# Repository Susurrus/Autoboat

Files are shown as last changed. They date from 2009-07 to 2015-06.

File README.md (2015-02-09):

Autoboat
========

This repository contains code used for running the Autoboat, a 20' robotic surface vessel currently in development at the University of Santa Cruz under the directive of Professor Gabriel Elkaim. This respository is therefore likely to be of little interest to outsiders, though much of the support code is fairly modular. Groundstation software for this vessel is provided via the QGroundControl project and is not contained within this repository.

File layout
-----------
 * CAD - Contains CAD designs of both mechanical and electrical systems. The mechanical systems have been modeled in SolidWorks 2010 while the electrical schematics have been generated using Eagle 6.
 * Code - This contains the software used for controlling the boat. Primarily Simulink and C control its operation and MATLAB and Python scripts assist in data parsing and analysis
 * Documentation - Various documents regarding this project are stored in this directory.

Main project
------------

The main project code is housed within /Code/Primary_node/primary_node.mdl and /Code/basic\_model/Boat\_sim.mdl, both Simulink 2011b models.

Boat_sim.mdl provides a simulator for testing my vehicle/environmental model and the vehicle controllers. It can run solely on a computer or via a UDP port provide the vehicle/environmental simulation to an external controller for use in Hardware-in-the-Loop (HIL) testing. Relies on the MicroSimulink library (<https://github.com/Susurrus/MicroSimulink-Library>).

primary_node.mdl contains all of the controller logic for the primary controller. It is organized as hardware dependent code that wraps the main controller block that is shared with Boat_sim.mdl (via the make.m script). This is designed to run aboard a CANode with the dsPIC33FJ256GP710A onboard along with a custom shield for providing connections to peripherals. It depends on both the MicroSimulink library (<https://github.com/Susurrus/MicroSimulink-Library>), Lubin's PIC blockset (<http://www.kerhuel.eu/wiki/Simulink_-_Embedded_Target_for_PIC>), and the ECAN blockset (<https://github.com/Susurrus/ECAN_dspic>). All of these dependencies must be correctly installed and on the path along with Microchip's xc16 compiler for this project to compile to an executable.

The toolboxes required by the various models are the Aerospace Blockset, MATLAB, MATLAB coder, Simulink, and Simulink Coder.

Code generation of the MATLAB projects requires a supported compiler [www.mathworks.com/support/compilers/R2011b] crosoft's Visual Studio 2010 is also required in order to compile the project or the Windows SDK 7.1 or newer. Both are available for free online.

In addition to these Simulink libraries, the MAVLink C library for the SeaSlug must be installed. Download it from <https://github.com/mavlink/mavlink> into the same directory that this repository is contained in so that it looks like:
/MicroSimulink-Library
/ECAN_dspic
/Autoboat
/mavlink

You'll need Python 2.6+ to run the MAVLink generator from within the mavlink directory:

```$ python mavgen.py --lang=C --wire-protocol=1.0 -o include ../Autoboat/Code/Libs/MAVLink/seaslug.xml```

This will put the MAVLink code for the SeaSlug dialect into ```/mavlink/include``` where it can be referenced by primary_node.mdl.

The current version of MAVLink will not compile with the xc16 compiler unless the ```stdint.h``` header file within the xc16 includes directory is duplicated as an ```inttypes.h``` file.
 
Further documentation
---------------------

A wiki has been hosted to provide details on this project at <http://byron.soe.ucsc.edu/autoboat/wg2/>.

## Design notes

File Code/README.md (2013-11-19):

1. Introduction
===============

This folder contains various projects containing code pertaining to the SeaSlug.

2. Requirements
===============
Software:
 * MATLAB/Simulink
     * Instrument control toolkit/blockset
     * Aerospace toolkit/blockset
     * Embedded coder, MATLAB coder, Simulink coder
     * [uSimLib](https://github.com/Susurrus/MicroSimulink-Library) and in the path
     * [Lubin Kerhuel's Simulink blockset](http://www.kerhuel.eu/wiki/Simulink_-_Embedded_Target_for_PIC) and in the path
     * Added to the path: `/Code/Libs/MATLAB`, `/Code/primary_node`, `/Code/basic_model`, `/Code/Scripts/MATLAB`
 * Microchip's MPLAB X (newest)
 * Microchip's XC16 (newest)

Hardware
 * CANode (contact asl.soe.ucsc.edu) with dsPIC33EP256MC502

3. Projects
===========

basic_model
-----------
Implements several simulator models along with Plant.mdl, the plant used for simulating the boat. Utilizes a crude inverse-bicycle model. To run these `/Code/primary_node/` must be on the MATLAB path. The `/Code/basic_model` folder must also be on the path for opening these models when the current working directory is not this folder.

HIL_node
--------
Provides a CAN interface with the basic_model simulator via a serial connection (that needs a serial-to-UDP bridge). Emulates many of the other nodes in order to fool the primary_node into normal operations. Written in all C.

Imu_node
--------
Provides a CAN interface to the Tokimec VSAS-2GM IMU+GPS interfacing over RS232. Broadcasts all incoming IMU data via CAN using the same data packets the VSAS-2GM would normally use over CAN. Utilizes Lubin's blockset for generating C code from Simulink.

Libs
----
Contains all shared code used by this project sorted by language. Also contains input files for some libraries, like MAVLink.
 
Paper_sim
---------
A simulation model built off of P�rez and Blanke 2002. Relies on many coefficients that need to be found experimentally, so it's not very accurate right now. Hopefully this will be the approach taken for the final boat model.

Power_node
----------
This runs on a CAN node and translates the sensor values for the current/voltage sensor on the main power rail into CAN messages. These are then processed by the primary controller node. Written entirely in C.

Primary_node
------------
This node implements the same controller as the basic_model simulator. It has an onboard interface to an analog power sensor, but otherwise all vessel communications are done over CAN. Its groundstation output is via the UART connector on the CANode.

Compiling this code involves generating the code for controller.mdl using Simulink (requires github.com/Susurrus/MicroSimulink-Library). Then all necessary C code is compiled using MPLAB X.

Additional requirements for compiling this node:
 * The XC16's `stdint.h` file should be duplicated as the `inttypes.h` file in order for MAVLink to compile.
 * It requires a SeaSlug-compiled MAVLink library, generated by the mavgen.py tool from github.com/mavlink/mavlink using the .xml file in `/Code/Libs/MAVLink`.
 * A heap size of 1024 bytes should be specified when the project is compiled in MPLAB X.

RC_node
-------
Provides a CAN interface for an RC receiver using a CANode. It also has a custom shield providing a plug-in interface for Spektrum's AR6100e receiver. Relies on Lubin's blockset for code generation.

Rudder_node
----------------
Integrates with the rudder (a stepper motor driver board, potentiometer position sensor, and port/starbord limit switches) and provides a CAN interface to it. Handles calibration as well. This has the same compilation requirements as the RC node.

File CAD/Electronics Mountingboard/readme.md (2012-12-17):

# Electronics Mounting Board

This directory contains Solidworks 2012 CAD files for a mounting board for the various onboard electronics onboard the boat. It fits inside a Wiegmann BN4161406SS electronics box. This includes a large capacitor, 3 CAN nodes providing various functions, and an ACS300 brushless DC motor driver board. Some screw terminal blocks also have mounting holes (they're all from Blue Sea Systems).

It was designed to be cut out of a non-conductive 1/4" material. The Corel Draw DXF file is included for use with a laser cutter.

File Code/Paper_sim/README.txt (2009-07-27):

This is a boat model based on the following paper:

Pérez and Blanke. Mathematical Ship Modeling for Control Applications.  (2002) pp. 1-22

This model uses constants defined in boat_constants.m as the coefficients for the boat dynamics. Most of the 
constants are currently made up or loosely approximated (eg. the intertias are based on a cuboid roughly the 
volume of the boat).

Currently the model tops out at 1.93m/s when at maximum throttle. This model is stable.

There are many properties of the boat that need to be experimentally determined to improve this model and are 
listed under the experimental constants in boat_consants.m.

The model Currently only implements a couple of forces/moments:

Drag (Using wg1 sim model)
Thrust (Using wg1 sim model)
Rudder moment (using wg1 sim model)

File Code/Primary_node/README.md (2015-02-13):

## Compilation

Compilation is done in two stages: first by MATLAB/Simulink and finally by MPLAB X. The first stage involves code generation (see the project README for software requirements). The second stage with MPLAB X involves compiling the resultant MPLAB X project and manually setting the Memory Model to 'large'.

This project requires both the '/Code/Libs/MATLAB' folder and the MicroSimulink-Library project be added to MATLAB's path to compile.

### MPLAB X Project Settings
 1. Add the following directories to the include search path: 
   * `/Code/Libs/C`
   * `/Code/Libs/MAVLink/seaslug`
   * `/Code/primary_node`
   * `/Code/primary_node/controller_ert_rtw`
 2. Specify the large code & large data model
 3. Add "MAVLINK_ALIGNED_FIELDS=0" as a C macro
 4. Add MAVLINK_SEPARATE_HELPERS as a C macro
 4. Add all *.c under `controller_ert_rtw' to the project.
 5. Add all *.c files in `/Code/primary_node`.
 6. Add missing files as reported by the compiler in `/Code/Libs/C`
 7. OPTIONAL: Add traps.c if weird resets occur to see which error is triggering
 
Note, when regenerating MAVLink, there may arise a conflict between the mavlink_helpers.c file we provide and the function prototypes provided in protocol.h. The mavlink_helpers.c file will need to be adjusted by just copying over the functiond definitions from mavlink_helpers.h.

### dsPIC33E versus dsPIC33F

Switching between these processors requires the following changes:
 1. Choose the proper DEES_*.s file based on the processor type selected.

## Functionality

### MAVLink corruption compensation
The UART1 transmission is connected to UART2 reception at the pin-level on the PIC. A separate MAVLink decoding process is run on this and the processor logs when its output stream has become corrupted, resets the UART1 transmission hardware and outputs a STATUSTEXT MAVLink message with the time this occurred.

Additionally, while the data stream is corrupted, pin RB0 is set high, so a low value indicates a valid MAVLink stream.

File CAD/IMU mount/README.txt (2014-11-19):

This is a mounting plate for the Tokimec VSAS-2GM IMU onto the wooden IMU shelf in the forward compartment of the SeaSlug. 5/8" #8 wood screws fit in the outer-most screw holes securing the plate to the boat. M6 Allen-head bolts screw up into a locknut above the Tokimec.

This can be trivially lasercut out of acrylic. The #8 screws will need to be recessed and same with the boltheads for the Tokimec.

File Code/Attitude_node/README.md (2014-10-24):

Add all files in this directory along with:
  /Code/Libs/C/{CanMessages.c, CircularBuffer.c, Ecan1.c, MessageScheduler.c, Node.c, Timer2.c, Stack.s, Traps.c, Uart1.c}
  /Code/Libs/MPU60xx/*.c

You need to make sure `git submodule init` and `git submodule update` were run and that `/Code/Libs/MPU60xx` exists with code inside.

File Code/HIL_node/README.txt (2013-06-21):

This code implements a CAN to UDP bridge for use in HIL simulation. It runs atop  a CAN node with a ENC28J60 Ethernet shield. It emulates all CAN-based sensors and sits between the primary controller for the SeaSlug and its Simulink simulation.

This code builds on the TCP/IP stack provided by Microchip and available directly from them. While none of their library code has been modified for this project, it has been included here to simplify things.

# Usage
This code should be compiled for the CAN node and programmed onboard. That node should have an ethernet shield and be connected to a laptop (it has a DHCP server so IP address assignment is automatic) as well as to the primary controller node via CAN.

# Compilation

Compilation is done completely via Microchip's MPLAB X IDE and the XC16 compiler.

Required include directories:
 ./TCPIP
 .
 ../Libs/C 

Required source files:
 ./*.c
 ./TCPIP/TCPIP Stack/*.c
 ../Libs/C/[Acs300,CanMessages,CircularBuffer,Ecan1,MessageScheduler,Nmea2000,Nmea2000Encode,Node,Rudder,Timer2,Timer3,Timer4].c

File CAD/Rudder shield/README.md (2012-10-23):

This board is designed for V2.x of the CAN node that exists in the ASL repository. I provides connections for integrating an analog potentiometer (with a 21Hz lowpass filter on it) and two open-drain limit switches. Additionally it has a connection for a stepper motor driver board.

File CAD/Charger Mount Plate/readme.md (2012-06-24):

# Charger Mounting Plate

This directory contains the Solidworks 2008 CAD designs for a electronics mounting board for use in the bow of the Autoboat. A Corel Draw file is included for the mounting board itself for use with a laser cutter.

This board is designed to be laser cut out of 1/4" material, preferably something that doesn't respond to moisture like acrylic (not MDF). It's used for mounting both a Wiegmann BN4161406SS electronics box as well as the Dual Pro Professional Series Quad Pro battery charger. It is designed to be mounted in the boat with the charger mounted on the left side. 

This board should then be attached to two 2x4s that run along the entire width with the 4" against the MDF. For each of the mounting holes in the MDF, 3/4" holes should be drilled through the 2x4s to allow for a socket wrench.

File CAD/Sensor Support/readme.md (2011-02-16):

= Sensor Support =

This directory contain Solidworks 2008 CAD files for a truss support for the CTD sensor payload in use with the Autoboat. It is designed to fit between the boat deck and the top rung of the sensor payload. Four of each truss should be manufactored (designed for 1/4" MDF and for laser cutting) and fit together in duplicate to make a square. Zip ties fit through the top little slits to hold it to the payload.

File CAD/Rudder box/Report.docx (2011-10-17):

Chris Hui

ASL

Rudder Box Report

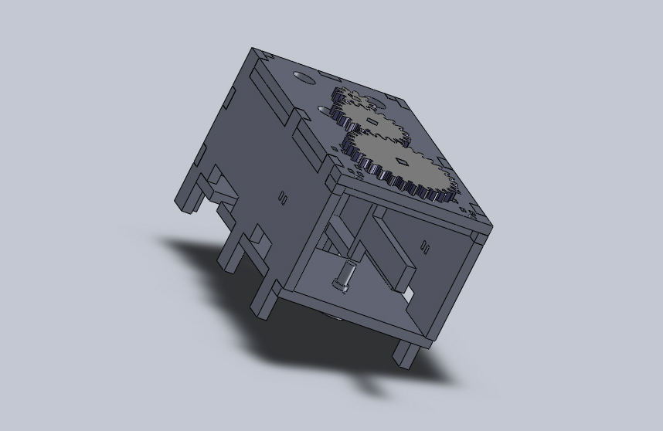
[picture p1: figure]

Fig. 1: Rear View of Finished Rudder Box Assembly in SolidWorks

/ / This paper, written from 8/23/2011 to 9/1/2011 (10 days), is an attempt to document as much of the design and construction process that went into building the rudder box which we worked on from 7/18/2011 to 8/22/2011 (36 Days). It is intended to be able to convey exactly what we did, why we did it, and how we did it to someone somewhat familiar with basic CAD, laser cutting, and/or manual assembly. / /

Table of Contents

I. About . . . . . . . . . . . . . . . . . . . . . . . . . . . . . . . . . . . . . . . . . . . . . . . . . . . . . . . . . . . . . pg. 1 - 2

II. Making . . . . . . . . . . . . . . . . . . . . . . . . . . . . . . . . . . . . . . . . . . . . . . . . . . . . . . . . . . . . pg. 3 -

III. Our Thoughts . . . . . . . . . . . . . . . . . . . . . . . . . . . . . . . . . . . . . . . . . . . . . . . . . . . . . . . pg. 6 -

[1] About

a) What did we do:

We built a model rudder box that replicates the rudder box of a boat of ours on a smaller, portable scale. Basically, what we did was build a 4 inch by 8 inch box with an open back that's designed to fit a gear train on its top, and a small motor and rudder inside. We then finished our setup by putting 2 LEDs, 2 magnet sensors called Hall Effect Sensors, and a magnet in the mix. The result is a portable rudder box capable of serving as a robust rudder angle test platform.

b) Problem:

Before we had built this rudder box, we had to constantly go back and forth between our lab and an outside parking lot, where we have our physical boat located, if we wanted to conduct any live tests involving an actual rudder on the control algorithm we've been designing for our boat's autonomous rudder system. Typically, such a trip would involve wasting a lot of time and energy moving a lot of equipment in an out, as during testing we might discover hardware or software bugs that can only be fixed with equipment we might have left back in lab. One small incident like that could stop testing for a good 20 minutes. And for a long term project like ours that is projected to span several years, that's not a good thing. If we could do all our live rudder testing in lab somehow, that would save us a great deal of trouble.

c) Our Answer:

Since all we were doing when we went outside to conduct live tests on the boat's rudder control algorithm was hook up a computer to the boat's rudder system and send data that should (if everything is working right) move the rudder either right or left by "X" degrees (where X is a variable controlled by the data we send) and create a resulting rudder angle which we expected; we figured we could just make a scaled-down replica of our boat's rudder system and just run our computer programs on that. What we ended up building was a small rudder box capable of testing the control algorithm responsible for autonomously controlling our boat's rudder angle.

d) Why?

We decided to do things this way for two reasons outside the fact that we knew it could get the job done. First of all doing it this way made the final product really easy to envision, as all we would be doing would be a scaled down replication. Replication would only require that we have knowledge of what parts are going to be involved in building the rudder box, and how we might reproduce those parts. With all of the parts involved (a box, motor, gear train, rudder, potentiometer) being relatively easy to understand, and either available lying around our lab or possible to construct using a laser cutter (which we have), it's a very straightforward job.

The other reason why we decided to do things this way, is that it would provide a gentle introduction for someone new to our lab to learn how to 3D model, laser cut, and work with basic electronics by getting a chance to use all those skills in actual product design.

[2] Making

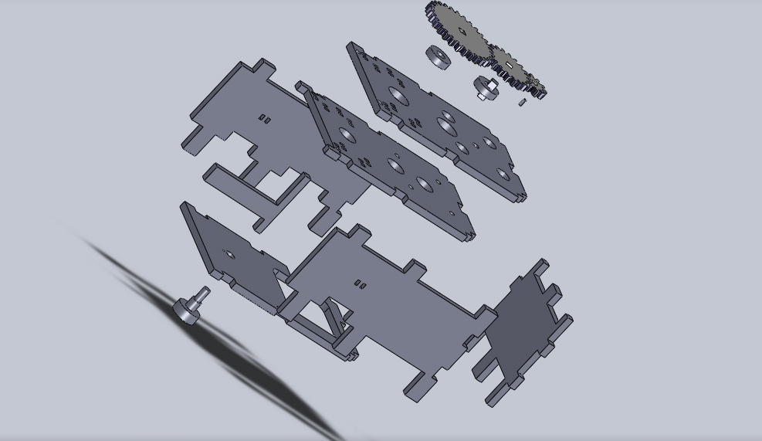
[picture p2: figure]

Fig. 2: Exploded Side View of Rudder Box Assembly in SolidWorks

a) Overview:

The gearbox was realized through a four-step process involving CAD, Laser Cutting, Assembly & Testing, and Redesign (which starts the whole process over again in what we a "reiteration"). Our design went through a lot of such reiterations before we were finally happy with what we got. Directly below this section is a barebones cookbook approach to building our rudder box. What it doesn't talk about is the history of how we got there. That we'll save for later, when we starting talking about the specific redesigns we made on this product towards the end of this section.

Process:

I. CAD

1. Draft Design on Paper

2. Measurements Using Calipers

3. Model Pieces in SolidWorks

II. Laser Cutting

1. Laser Cut Pieces

1/4" Foamcore Pieces (Optional - Testing)

1.-11. All

1/4" MDF Pieces

1. Top 1

2. Top 2

3. Side w/ Port

4. Side

5. Front

6. Bottom

7. Rudder

8. Rod

1/4" Acrylic Pieces

1. 10 Gear

2. 20 Gear

3. 30 Gear

III. Assembly

1. Wood Glue Box

2. Screw In Motor

3. Put in Washers

4. Fix Gear Train

5. Place LEDs

6. Wire LEDs

7. Tape Hall-Effect Sensors

8. Zip Tie Hall-Effect Sensors

5-8. Test LED/Hall Effect Sensors Using Breadboard (Optional - Testing)

9. Fix Potentiometer

10. Heat Shrink Rudder

11. Tape Magnet to Rudder

11. Test Magnet/LED/Hall Effect Sensor Setup (Required -Testing)

12. Hot Glue Gears

b) Part 1: CAD Design

Using:

- Pencil and Paper

- Calipers

- SolidWorks 2010

The main program we used for our CAD drawings was SolidWorks 2010. We used it to determine the dimensions of all the extruded pieces we need to have cut out as well as some pieces we don't need to have cut but would like to model anyway just to see how things fit. But before we drew anything in SolidWorks, we drew it on paper using pencil.

First drawing a rough sketch of what we wanted, we then took measurements of the parts we knew we would be using straight from the shelf, around which we would be building the rest of our assembly. These pieces were the motor, potentiometer, LEDs, washers, Hall Effects, wire, screws, and magnet.

This means taking into consideration the sizes of these pieces when designing the box which is supposed to contain them. If this step was done well in the beginning we could have very well cut our production time down by approximately 60% (as that was roughly how much time was spent reworking parts measurements in CAD). Knowing exactly what you want saves a lot of time. We should have only begun modeling parts in SolidWorks only after having a clear layout of what we're trying to model in front of us.

After getting all their measurements correct, drawing the 11 Pieces in SolidWorks one at a time is a piece of cake. All it is really, is designing the 6 pieces of the box, 3 gears using Gear Template, and a rod and rudder that all fit together where they are supposed to. If the measurements were done correctly everything would just fall into place. The pain of SolidWorks comes from trying to make fixes in the program, as often if one thing is off it usually takes fixing more than just that one thing to get what you want.

The SolidWorks skills required for this particular project are actually quite basic: all you need to know is how to make shapes, extrude them, make extruded cuts, smart dimension, mate in assembly, and if you want to get fancy use fillet and/or explode like we ended up doing. All this can be easily learned via the SolidWorks tutorials. Again, the hard part is working with measurements. Everything has to fit perfectly.

The way to check if everything fits is to take all the individual parts and combine them in a SolidWorks Assembly. After mating everything together, if they fit the way they are supposed to everything's good to go. Taking care to make sure that they actually fit in SolidWorks can also save a lot of time. It's imperative you check that there are no overlaps (as SolidWorks will let this happen without alerting you) or gaps.

If we had done it correctly the first time it could have very well saved us 20% of the time we spent. Laser cutting takes time, and laser cutting a faulty assembly and then trying to assemble it only to find it halfway through assembly that something isn't right forces us to stop what we're doing and make premature reiterations that might better be saved for later when we've got more changes to make.

With the assembly looking then good, we try to brainstorm any improvements that we could possibly make to it. Thinking up these possible upgrades before doing any laser cutting also saves a lot of time and can cut down the number of reiterations you have to make significantly.

On this project, We had a tendency to only think up of only one upgrade per trip to the laser cutter and that made us take around 6 or 7 reiterations when really we should have only needed half as many in order to get the same results. Just committing to think of two upgrades per reiteration instead of just one would have saved us a considerable amount of time and raw material.

When we're finally ready to cut, what we do next is put all our individual parts into a SolidWorks drawing file as 2D shapes and then position all the shapes close together without overlap as close to the edge of the top right corner as possible before saving it as a .DXF file.

Below are the 11 parts we designed in SolidWorks (and their specs) that need to be cut for the rudder box. Unlabeled sides have a corresponding labeled side with the measurements either in the drawing of the same piece or a similar piece.

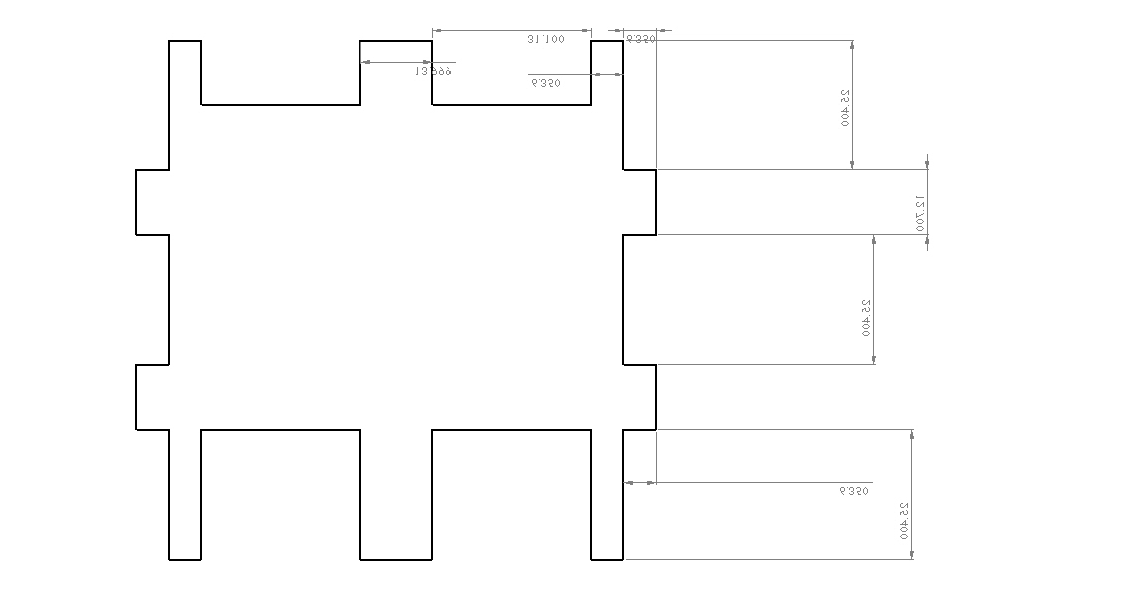
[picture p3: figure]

Fig. 3: Front

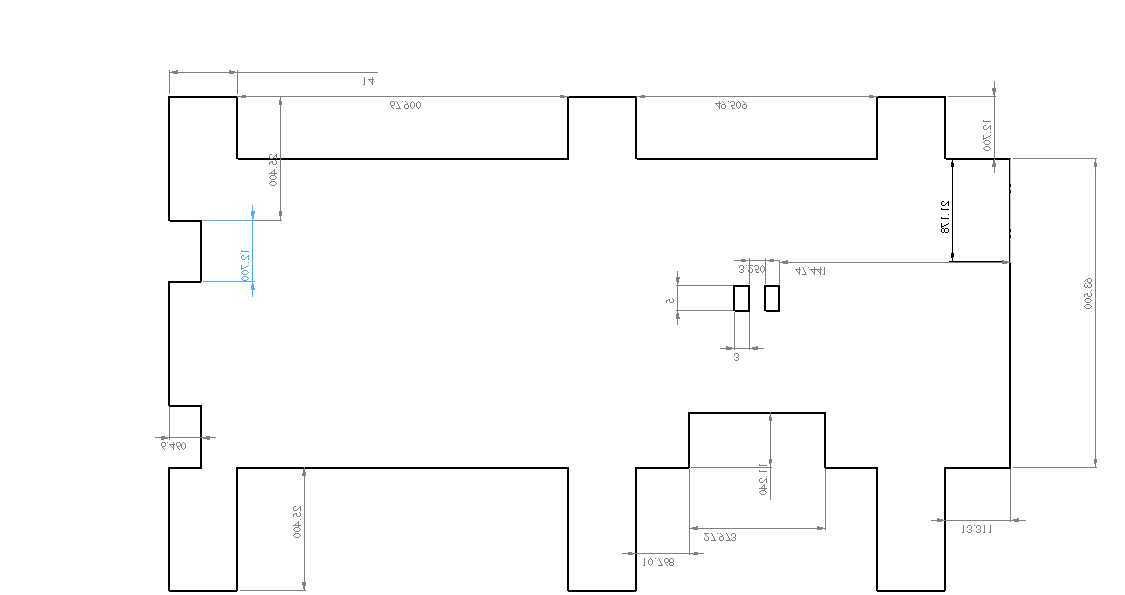
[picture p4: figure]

Fig. 4: Side

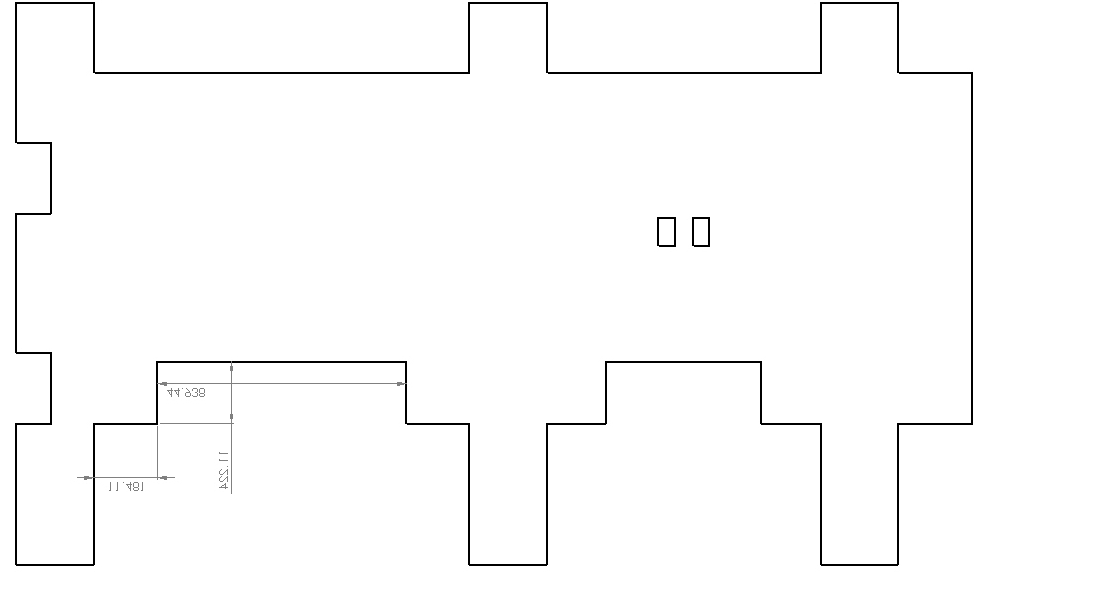
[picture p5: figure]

Fig. 5: Side With Port

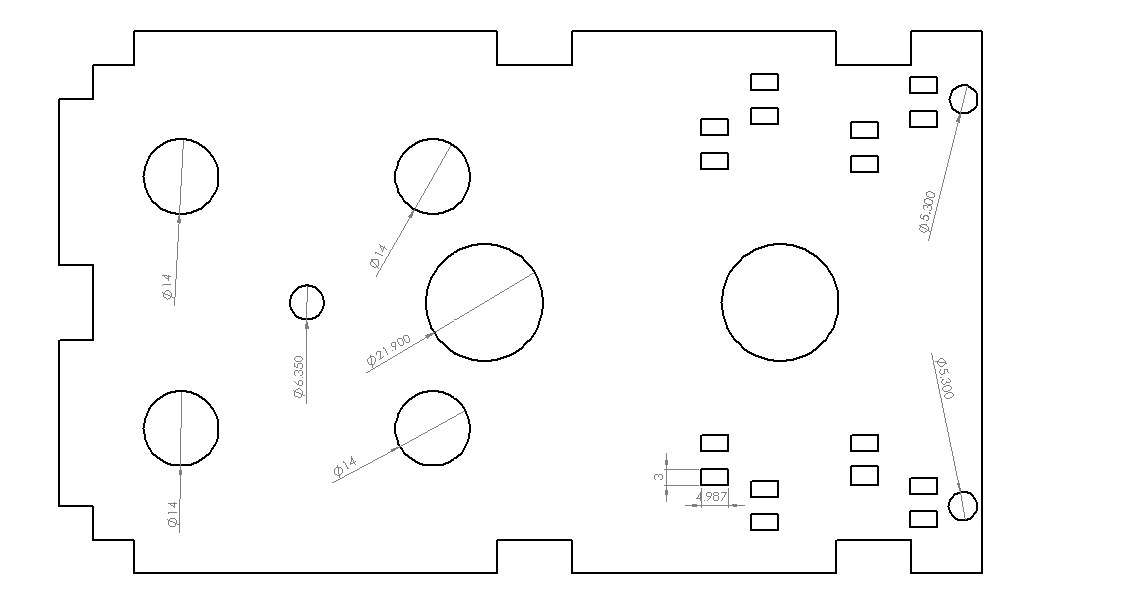
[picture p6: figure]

Fig. 6: Top 1

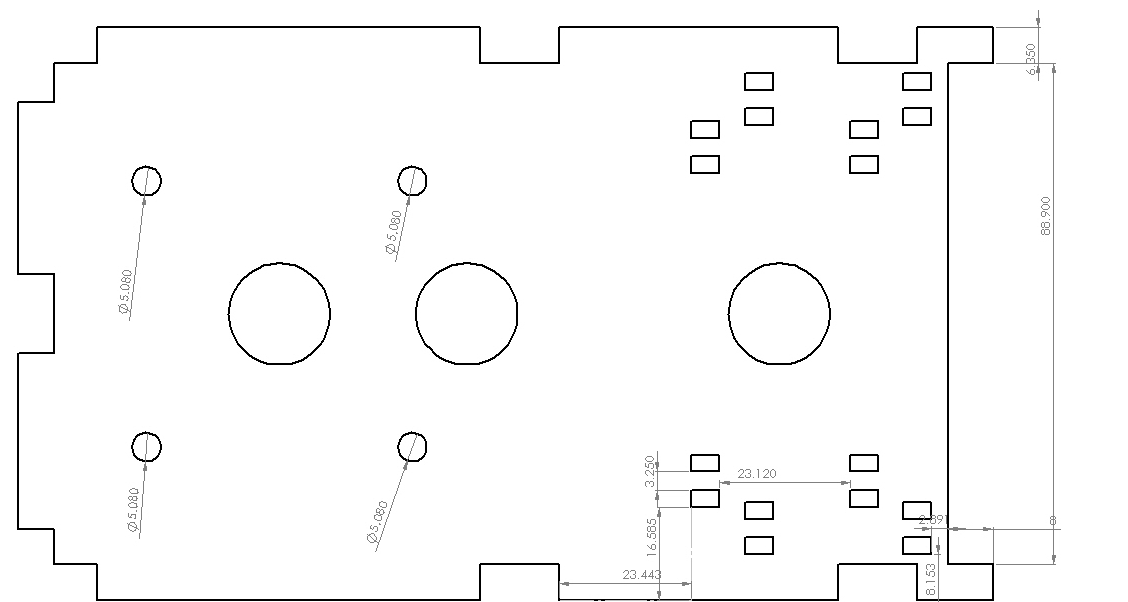
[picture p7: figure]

Fig. 7: Top 2

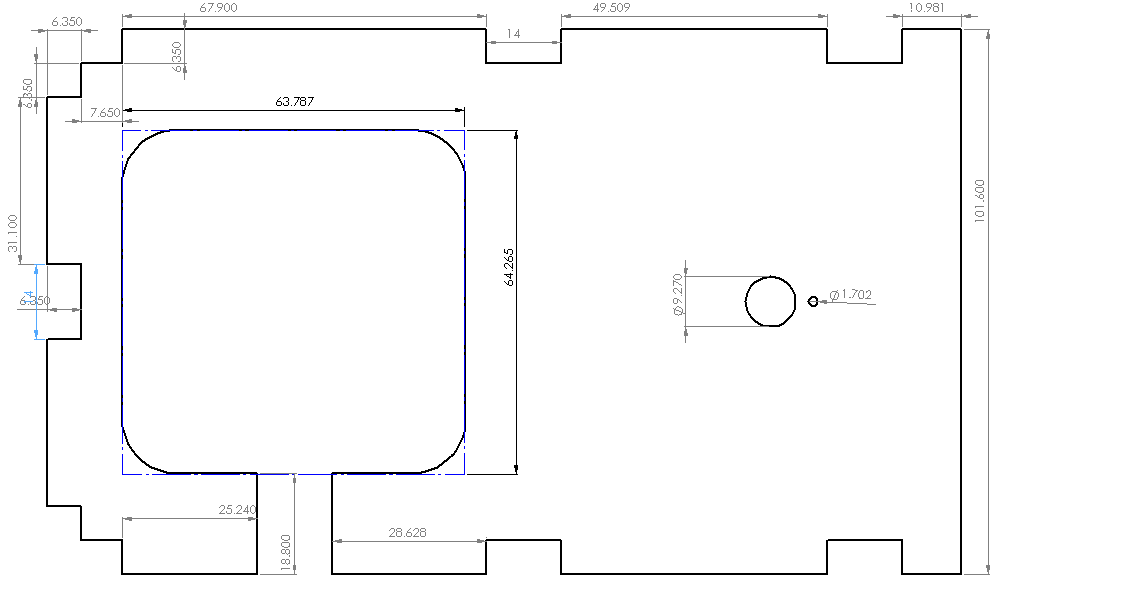
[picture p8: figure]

Fig. 8: Bottom

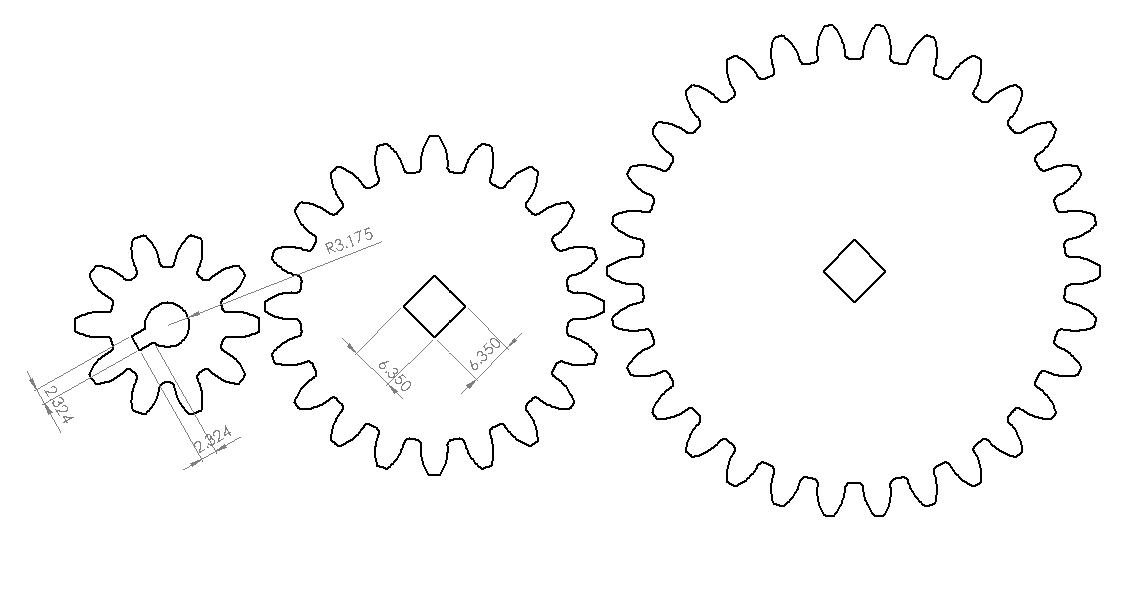
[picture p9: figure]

Fig. 9: Gear Train (Left to Right: 10 Gear, 20 Gear, 30 Gear)

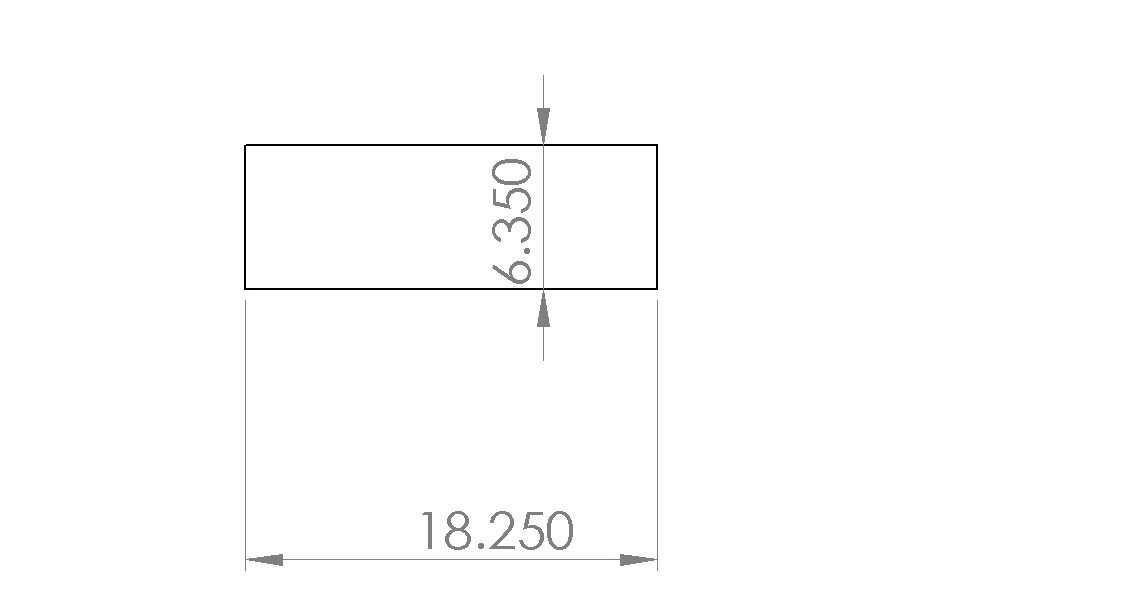
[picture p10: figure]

Fig. 10: Rod

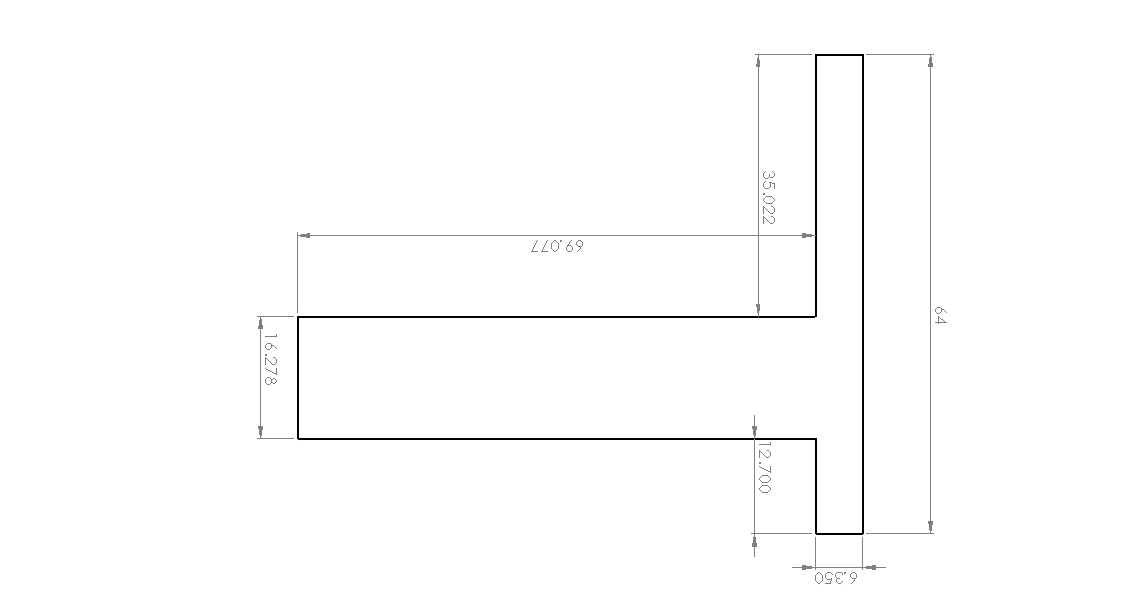
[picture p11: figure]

Fig. 11: Rudder

c) Part 2: Laser Cutting

Using:

- CorelDraw x4

- 30 Watt LaserPro Explorer II Laser Cutter/Etcher

- 1/4" Foamcore

- 1/4" MDF (Medium Density Fiberboard)

- 1/4" Acrylic

Having saved our Assembly as a .DXF file, what we do next is bring it over to another computer hooked up to our laser cutter and load it in CorelDraw x4. We do our laser cutting by printing it straight from there after putting our material in place and tweaking some printing properties.

Loading our Laser Cutter carefully consists of picking out a sheet of the material we want to use for the cut (making sure that it fits in the loading bay of the the laser cutter without hitting the carefully calibrated laser's head). After loading successfully we then fit as many 1/4" chips as it takes underneath the sheet we're cutting to keep the sheet it level. This is especially important with our laser cuter when cutting from a sheet that has already been partially cut. Such pieces are prone to bending when left on their own, doing this is the only way to ensure a clean straight cut. Putting the laser head right on top of the top left corner of the sheet we're about to cut we then autofocus the laser by pressing the auto focus button on our printer. This lets the laser know where the sheet is and allows it to adjust itself to the proper height to make a level cut.

Once we've got our sheet ready to cut, we can focus our attention on CorelDraw. The first thing we do is delete any crosses (that are not part of our design that appear over circles in our drawing). If we don't the laser cutter will mistakenly make extra cuts that waste power.

We then select all and change everything to red ink and thin line. This is important, for us to adjust the properties of the cut to fit the needs of the material and thickness we're using.

Pressing print, we then modify the printing properties according to the rules dictated by:

http://classes.soe.ucsc.edu/cmpe118/Winter11/LectureNotes/CMPE118_laser.pdf

We always change the settings to:

Under Pen Pen No. 2 (Red)

- Power: 100

- PPI: X

- Vector ON

- Air ON

- Raster Off

Under Advanced Settings

- Relative ON

- Vector Sorting ON

Power 100 cuts straight through, Vector cuts using lines, Air prevents the material being cut from catching fire by cooling it, Raser OFF ensures that the cut will not go back and forth along the same line, Relative makes the Corel Draw x4 top left corner start exactly where the laser beam starts, while Vector Sorting cuts parts inside out so that the piece doesn't fall out before it's complete (which sometimes gives uneven cuts).

As we are only dealing with 1/4" material, the speed we set the laser to depends on the type of material we are cutting:

for 1/4" Foamcore: 1.4

for 1/4" MDF (Medium-Density Fiber): 0.4

for 1/4" Acrylic: 0.5

Abiding by these speeds makes sure we get a clean cut that goes all the way through without burning the material.

For our design 8/11 pieces will be cut from MDF, and 3/11 from Acrylic. Initially when trying to put together a test model, we'd use Foamcore for everything which is cheaper and cuts faster.

MDF:

1. Front

2. Side w/ Port

3. Side

4. Bottom

5. Top 1

6. Top 2

7. Rudder

8. Rod

Acrylic:

1. Gear:

2. 20 Gear

3. 30 Gear

The reason we use MDF for the majority of our pieces is because is because it's proven to work for our laser cutter, and is strong enough for the job. The reason we use more expensive acrylic for our gears is that it cuts more smoothly and for pieces that we require to rub against each other a lot, the sliding effect that is produced by that smoothness guarantees longer service.

d) Part 3: Assembly & Testing

Using:

- Laser Cut Pieces

- Wood Glue

- Washers (x3)

- Hot Glue

- Motor

- Screws (x4)

- Screw Washers (x4)

- Vishay Potentiometer (x1)

- LEDs

- Zip Ties (x2 or x4)

- Hall Effect Sensors (x2)

- "Sockets" (x2)

- Wire (x10)

- Tape

- Breadboard

- Magnet (x1)

Once we have everything cut out, we can start gluing all the cut out pieces together just as we planned according to our SolidWorks assembly. Perfect for this job is wood glue, simply because just a little of it bonds MDF quite strongly. With our box complete, We can then put in our washers, LEDs, Zip Ties, and Hall Effect Sensors. After that, all we got to do is get our electronics wired together before finishing everything off by taping our magnet in just the right place.

For someone unfamiliar to where things fits these next few pictures might help. The final construction should look something like this:

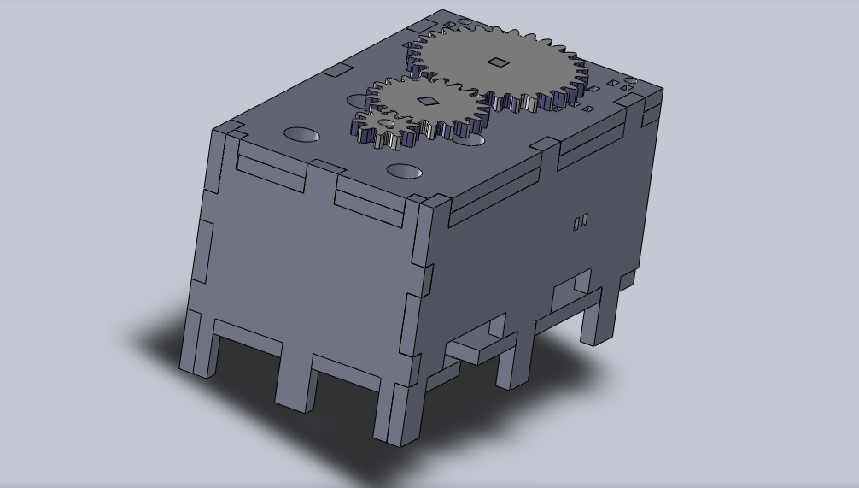
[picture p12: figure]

Fig. 12: Front Left Finished Rudder Box Assembly in Solid Works

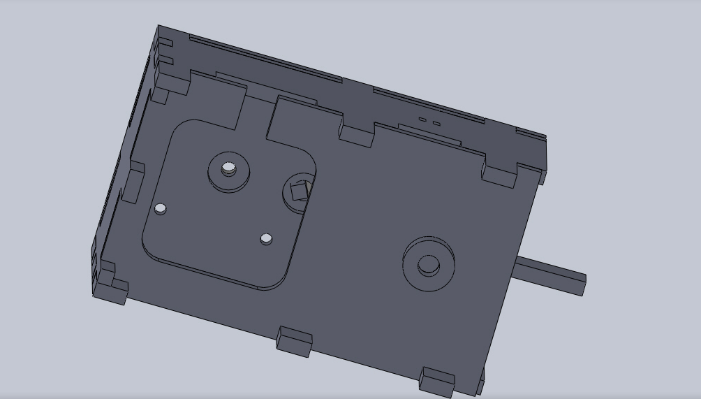
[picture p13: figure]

Fig. 12: Bottom View Finished Rudder Box Assembly in Solid Works

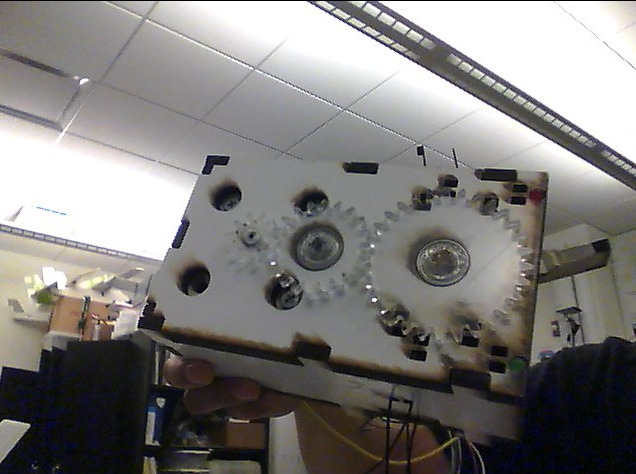
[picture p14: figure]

Fig. 13: Top View Finished Rudder Box

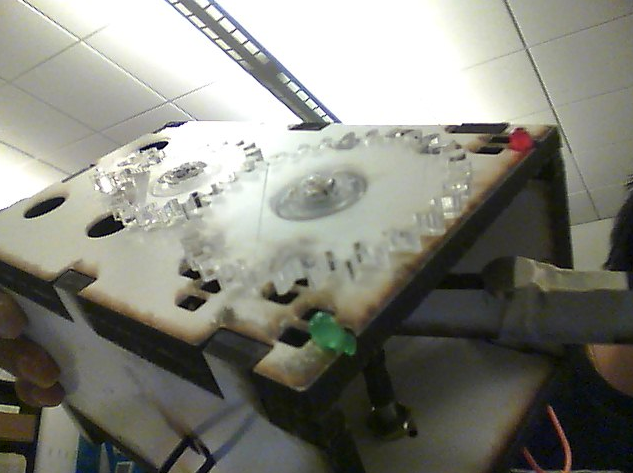
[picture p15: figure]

Fig. 14: Slanted Top View Finished Rudder Box

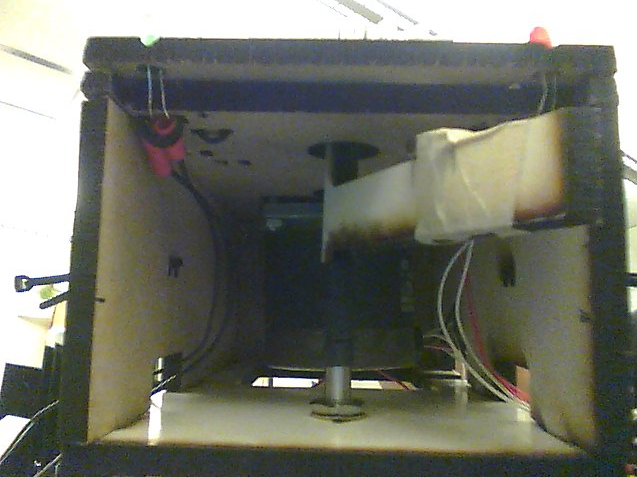
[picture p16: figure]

Fig. 15: Back View Finished Rudder Box

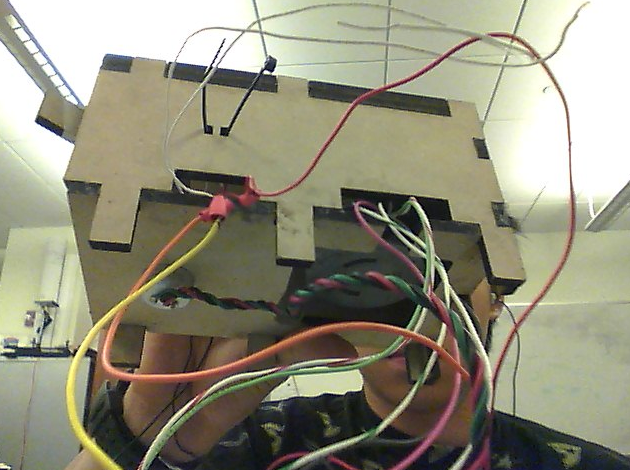
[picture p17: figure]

Fig. 16: Side With Port & Bottom Opening Connection

"Top 1" should be on top of "Top 2", and these should be flanked by the "Sides". Top 1 has two circle holes at one long end whereas Top 2 doesn't. These holes are where the LEDs mount (pictured as Red and Green in Fig. 13-16). Which side is the port side is determined by which side of the Bottom has the opening to the big square cut in it. They should both match up as pictured in Fig. 16.

All the edges of the box where one side touches another should be glued using wood glue. The motor should be shoved through the hole in the Bottom and secured by screwing it on top through both Tops. Washers should be put through the two holes where they fit on Top 1. The one rod should go through the middle one, while the rudder top should go through the back one (the back being the open end of the box). The top of the rod will be the longer part. Gears should then be placed on each of the three mounts (the 10 Tooth Gear at the front with the motor, the 20 Tooth Gear in the middle with the rod, and the 30 Tooth Gear at the back with the rudder).

Hot gluing the tops of these should be done later when the rudder has been set to the correct height. Do this as a last step after testing.

Once our box is assembled, and everything but the electronics have been set in place, we need to put those parts in with the magnet and test that it actually works. With our LEDs already in, we need to identify which one is the anode and the cathode, or + or - so we can wire our circuit according to this diagram that also includes our other electronic part (the Hall Effect Sensor):

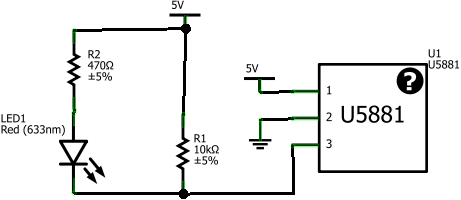
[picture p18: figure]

Fig. 3: Hall Effect Sensor Circuit Diagram

The anode is the longer leg, while the cathode is the shorter leg. Bending these legs towards the inside of the box, we can solder pieces of wire to these and put heat shrink over them and pull them through a port and wire them to a bread board.

We will be putting the heads our Hall Effect Sensors right above the backmost inside zip tie holds, with their metal rods pointing towards the inside of the box. The ziptie holes are the all the small cuts that permeate the back of Tops 1 and 2 and feature somewhat on the Sides. To secure our Hall Effect Sensors, what we do is put them each into a socket and tape it to the bottom of Top 2. Using Zip ties is optional, but if we want to use them we have to put it through from under and cut off excess zip tie, as tie it to the top like you might regularly do with a zip tie would impede our Gears.

Using Fig. 3 above as our guide we then wire everything together and connect the circuit into a breadboard.

What should happen is that one LED should light up every time it's corresponding Hall Effect Sensor detects the north face of a magnet. We want this to occur when the rudder upon which the magnet is mounted hits either extreme of 45 degrees right or left. Once we know our circuit is working, we can put a magnet at the back of the rudder and see about where it successfully does this (which turns out to be about the center). We can then tape it down, and if the LED above a corresponding Hall Effect lights up, when the Rudder has reached it's farthest extent to said side, everything will have been complete.

e) Part 4: Redesign

At this stage, we go back and make the adjustments in SolidWorks we've found that we needd to make using the same tools we used for parts 1-3.

When we did this project we had roughly 6 major reiterations according to the notebook we kept as we worked.

Reiterations:

Iteration 1: Open Back Box

What we first produced was four walled rectangular box with an open back.

Iteration 2: +Washer Holes, +Gear Train

We then cut 3 holes to allow washers to fit through the top of the box, and we also cut out a working three gear train.

Iteration 3: + Motor Holes, +Double Top, + MDF Gears to Acrylic Gears

After that we changed the front of the 3 washer holes and made it smaller for the motor head. We also added four holes for the screws to secure the motor. To help our gears stop slipping we added a second top as well that had holes slightly smaller than he top. We then changed our gears from MDF to Acrylic as that would help our gears move more smoothly.

Iteration 4: + Rudder, + Vishay Potentiometer Hole

We then added a rudder, and a hole for the Vishay Potentiometer as well as a model in SolidWorks.

Iteration 5: +Legs, + Side Ports, + Motor Easy Insertion Hole

To make room for the Potentiometer at the bottom, we raised the box so it would have stilts to stand on, we also cut side ports for wiring, and made a big hole in the bottom for easy motor insertion.

Iteration 6: + LED, +Zip Tie Holes,

The last thing we did was make room for our LEDs on Top by modifying our double top, with fitting configurations added, and a bunch of Zip Tie Holes for us to help secure our electronics.

Iteration 7 (to be done): + Rudder Groove Fitting Magnet, + Fitting Hall Effect Sensors, - Ziptie Holes

If we were to do one more reiteration we would cut a grove in the rudder for where the magnet is supposed to be, and a groove for the Hall Effects in Top 2 for where they are supposed to fit. That way there would be no need for making measurements during assembly. To remove unnecessary complexity from our rudder box we may opt to remove our zip tie cuts.

[3] Our Thoughts

a) Overview:

Designing and building what eventually became our final version of our rudder box took longer than it should have. It took about a month of many reiterations of CAD, laser cutting, and assembly before we were able to get what we now have, when really it should have taken a week to piece together. The reason it took so long was that the main person we had working on it came into the project knowing absolutely nothing about the techniques and processes involved and as a way of teaching him a great deal about our lab and the techniques utilized by our lab we had him try to improve his design with a new iteration each time he thought the job was complete.

By week one he had a working box in SolidWorks, that while lacking many of the intricacies of our later versions, could still with a few more cuts do a fine job as rudder box. It just needed holes for a rudder, screws for the motor, and room for the potentiometer at the bottom of the box. The motor could be put in first before the bottom, screwed in, and its wires could just pop out the back. Even though it wasn't the final product we wanted, we decided to get it cut out by the laser cutter anyway so the student could get more time in using the laser cutter, and could have a physical translation of the work he had done using CAD. We found the box to be acceptable and moved onto trying to get a 3 gear train as our next step.

Trying to make gears from scratch led us to try and find a gear template. It took us about a week before we finally found what we wanted and understood how to use it right by adjusting the ratio of # of teeth to pitch diameter. Getting up to speed on understanding the entire math behind building a properly constructed gear made any work done from scratch a non cost-effective solution.

Once we figured out how to do this, getting the three types of gears we wanted was easy, all we had to do was adjust a couple of numbers.

By week three we reassessed our design to be more ergonomic towards our gear train. We added a second top, and resized our washer holes so that the washers would fit under the 1st top so that between the rod and the gears there would be very low friction. The washers were friction fit to our top layer, and stopped from dropping with a little edge from the bottom one (Top 2). We then changed the material from which we cut our gears. We went from MDF to Acrylic because of its strength and more smooth surface. It's also from this point we adopted the technique of putting posts underneath the sheets we're cutting to ensure and clean/level cut. We also shifted between many different cuts for the screwdrivers, and changed the hole for our smallest 10 teeth gear to fit the motor. Once we were happy with that we started adding a rudder piece and potentiometer to the mix to see how much that would change our design.

The addition of these two elements necessitated for a lot more change than we'd initially anticipated. Needing to have a raised platform for the potentiometer to sit comfortably underneath the box, we had to make changes to our box that accidentally or unintentionally changed other things we didn't mean to change--resulting in a need to redefine and re-measure a number of the different relations that made up our box. By the end of the 4th week we had a better box that fit everything and even had a hole underneath the motor for easy insertion and removal after assembly

At this time the box was basically done, it could completely and comfortably route rudder angles, etc. etc. But instead of stopping there we decided at this point to add a Hall Effect sensing system with LEDs that would signal when our rudder hit either extreme of 45 degrees right or left. Adding this to the plan was consistent with our goals. It would have a practical application of lighting up whenever the rudder hit a full right or left turn, and second it would provide our "initiate" an introduction to working with electronic circuits.

At this point, came some playing around with and testing of Hall Effect sensors and learning how to read circuit diagrams and wire them in real life. Once we got comfortable understanding what we were working with we started moving in on getting it installed on our rudder box.

At this stage, entering our 5th week, we decided to make a bunch of little adjustments to fit the Hall Effect sensors and LEDs, aligning our rudder angle perfectly at 45 degrees, setting up ports for our wires to be able to get out without causing any interference to our rudder system, and to cut holes through both tops to make room for Zipties to secure our wires away from getting caught in the rudder. We made all the changes and found out that there were some complications surrounding the Zipties.

First of all it was very troublesome to perfectly aligning cuts along two different top layers, in CAD, it required measuring, drawing and re-measuring. Second, the Zipties couldn't be used without clipping off the tie and just using it to friction fit simply because the heads coming off the top ran into the 30 gear. And lastly, only two out of eight planned cuts were of any use, and even then only minimally to secure the head's of the Hall Effect sensors. Tape ended up working much better than Zipties without ties that kept falling out, so that's exactly what we ended up using.

With that and a little more testing, a little more confidence in our electronics, our rudder box was complete.

Overall we feel the job was a success, and though it could have been done faster, made up for itself by being both a useful product and a teaching aid to our new lab member.

b) Possible Upgrades:

If we were to do this whole project again it would probably have been completed in a week, spending different days to do different things:

Day 1: Drawing & Measurements

- Box

-- has to fit motor, washers, correctly spaced gear holes, holes for LEDS, wiring, potentiometer

- Gears

-- 3 correct ratios/distances

- Rudder

Day 2: CAD

- Box (6 pieces)

- Gears and Rod (4 Pieces)

- Rudder (1)

Day 3: Laser Cutting/Assembly

- Box

- Motor

- Potentiometer

- Rudder

- Gears

Day 4: Fixes/Assembly

Day 5: Wiring

- LEDs

- Hall Effect Sensors

- Wiring

It might take more time than this but this + or - some checking should be everything you need to construct a rudder box.

Upgrades:

There would be 3 places we'd like to make upgrades:

* Add notch for Hall Effects in Socket in Top 2

- This reduces the need to make measurements on where to put the Hall Effects

*Add notch in for magnet on top of the rudder to fit it's correct location

- This reduces the need to make measurements on where to put the Magnet

* Remove Zip Tie Cuts

- This gets rid of unnecessary features.

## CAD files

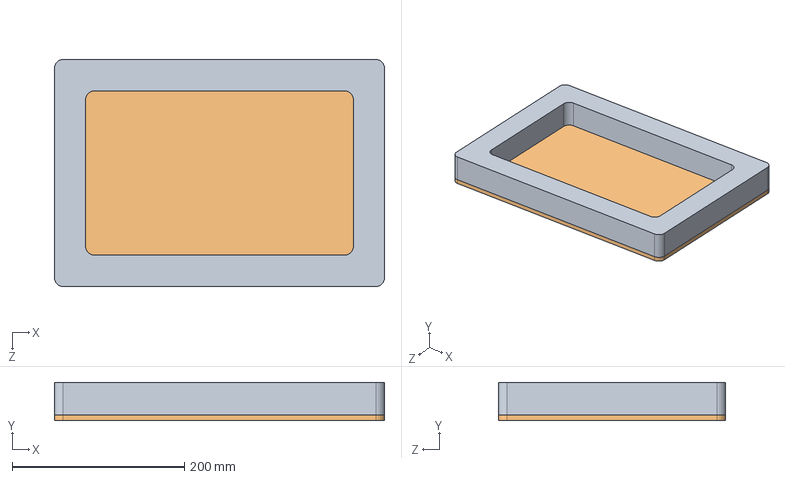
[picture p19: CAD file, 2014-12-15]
CAD/Groundstation mount/mounting.SLDASM
383.3 x 44.5 x 263.7 mm
foam_surround
mounting_board

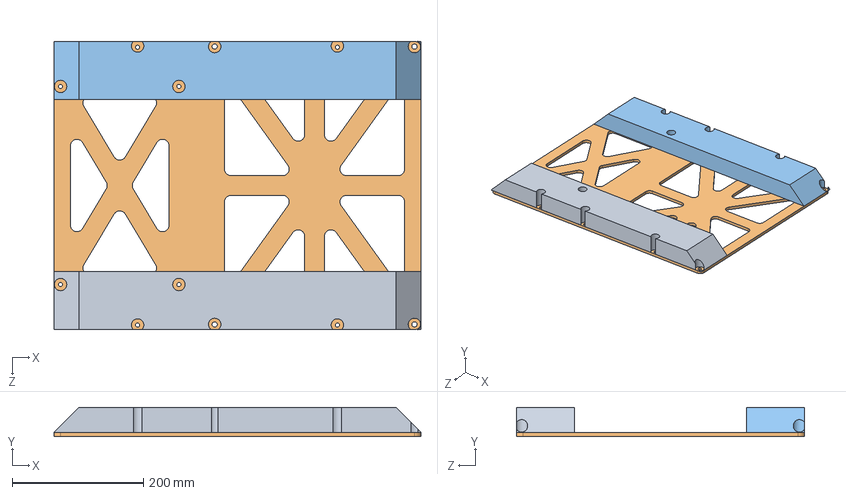
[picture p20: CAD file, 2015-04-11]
CAD/Charger Mount Plate/Complete unit.SLDASM
560.0 x 44.5 x 440.0 mm
Mounting plank top
Mounting board
Mounting plank bottom

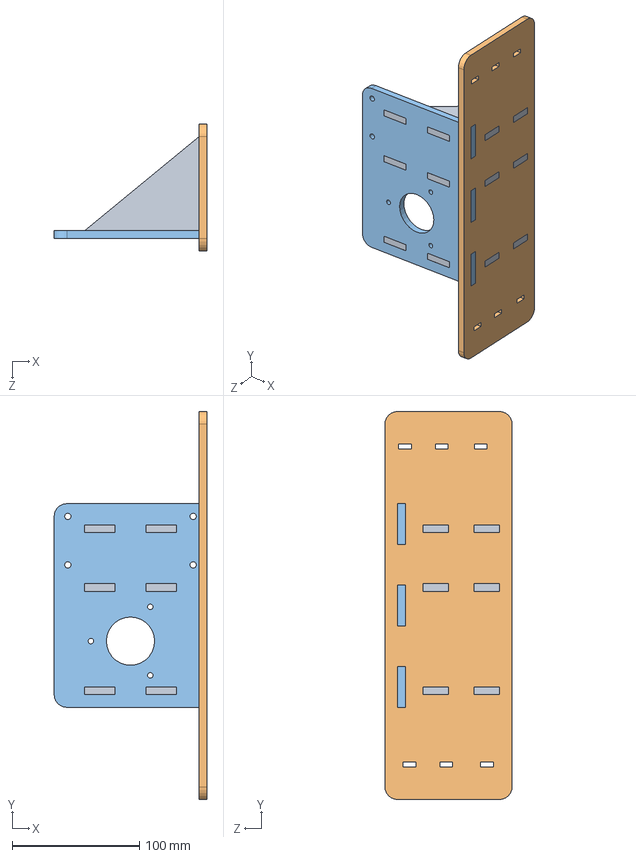
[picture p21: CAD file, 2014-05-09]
CAD/IMU tester mount/assembl.SLDASM
120.0 x 304.8 x 100.0 mm
brace x 3
chestplate
mounting board

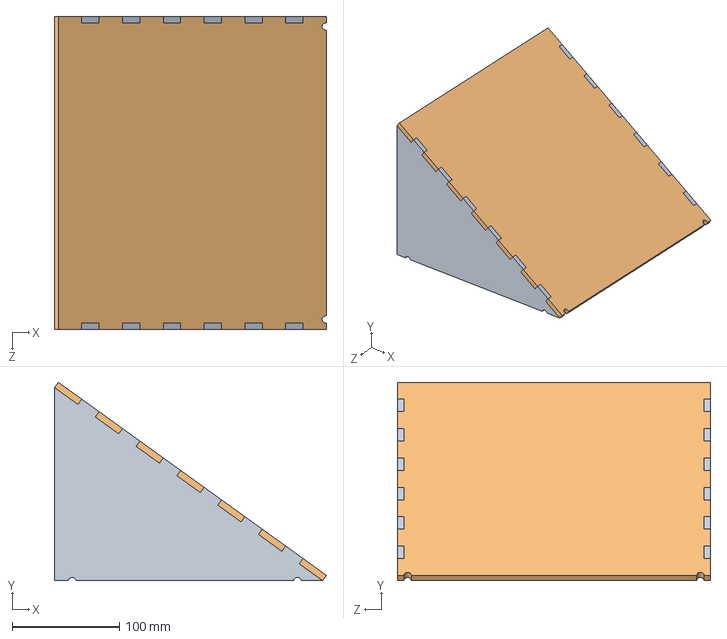
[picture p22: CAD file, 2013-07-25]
CAD/Pelican case/sunshield.SLDASM
253.6 x 184.9 x 292.2 mm
sunshield_sidewall x 2
sunshield_back

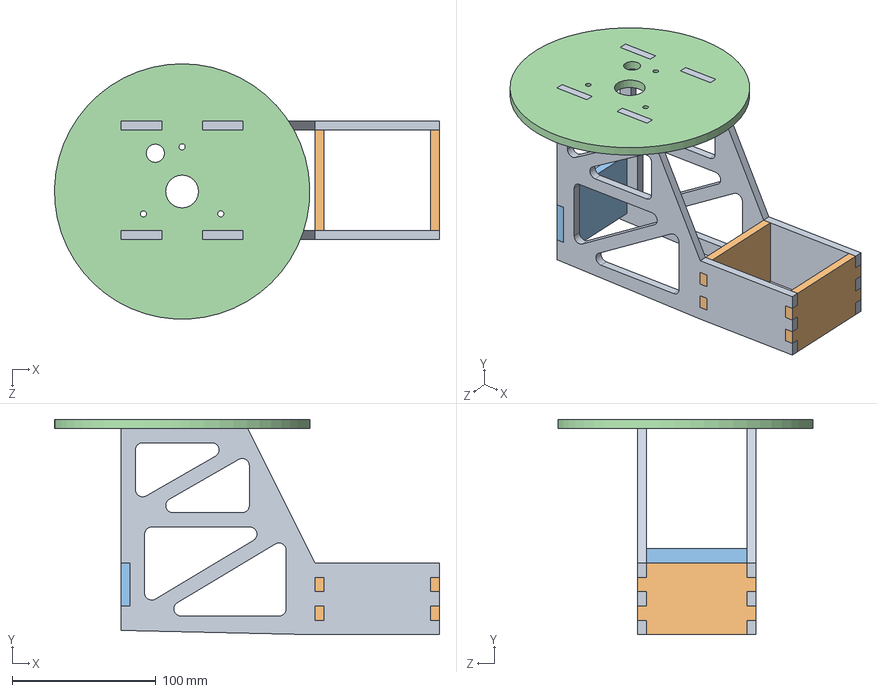
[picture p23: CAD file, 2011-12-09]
CAD/WSO100 Stub Mast/Assembly.SLDASM
268.1 x 150.0 x 177.8 mm
Large side x 2
Small side x 2
Cross support
Top mount plate

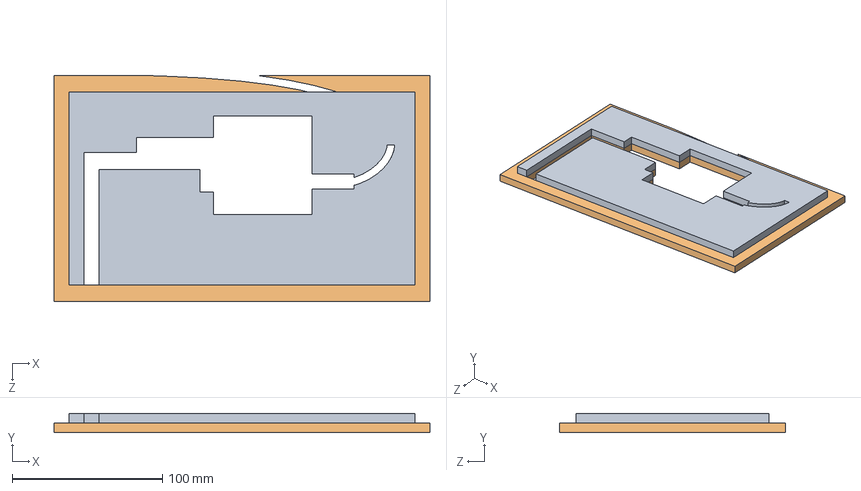
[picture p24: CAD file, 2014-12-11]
CAD/Groundstation mount/groundstation_backing.SLDASM
250.0 x 12.7 x 150.0 mm
Backing_top
Backing_bottom

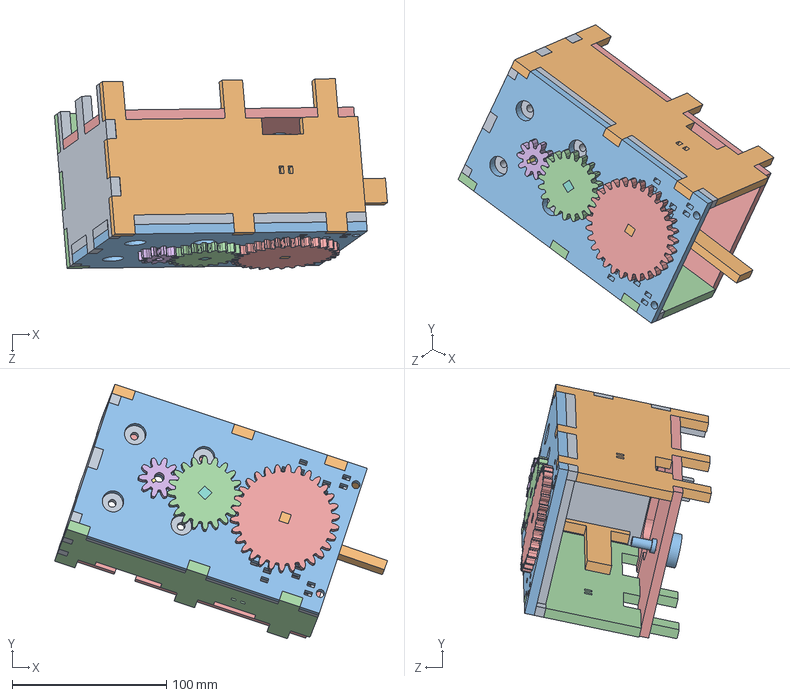
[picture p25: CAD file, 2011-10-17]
CAD/Rudder box/Assembly.SLDASM
216.2 x 165.3 x 123.8 mm
Front
Side
Top
20 Gear
30 Gear
10 Gear
Stopper
Rod
Top2
Rudder
Vishay Potentiometer
Side With Port (Legged)
Bottom
Washer x 2

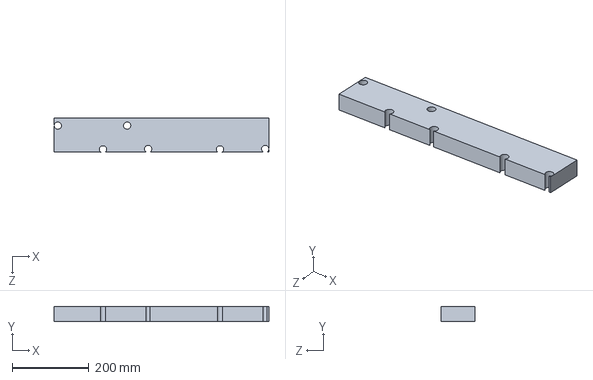
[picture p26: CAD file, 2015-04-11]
CAD/Charger Mount Plate/Mounting plank bottom.SLDPRT
560.0 x 38.1 x 88.9 mm

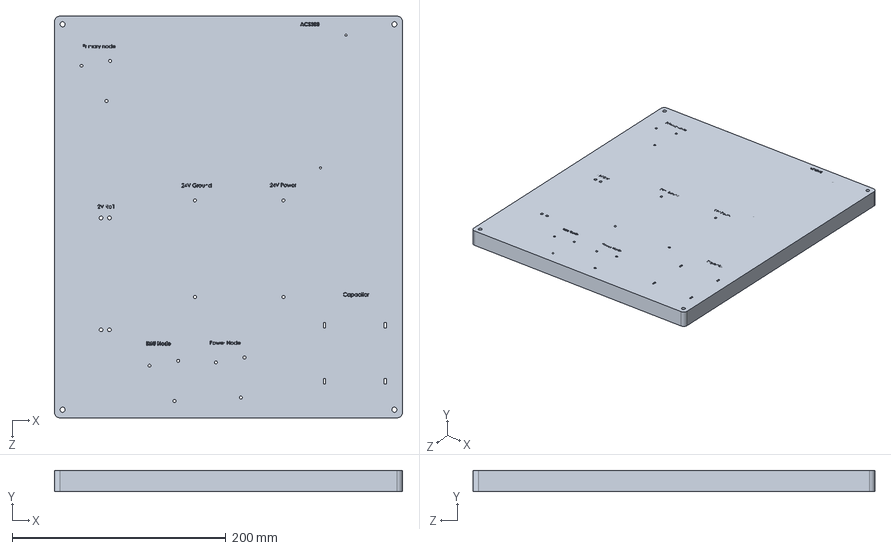
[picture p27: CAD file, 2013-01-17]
CAD/Electronics Mountingboard/mountingboard.SLDPRT
325.7 x 20.0 x 376.0 mm

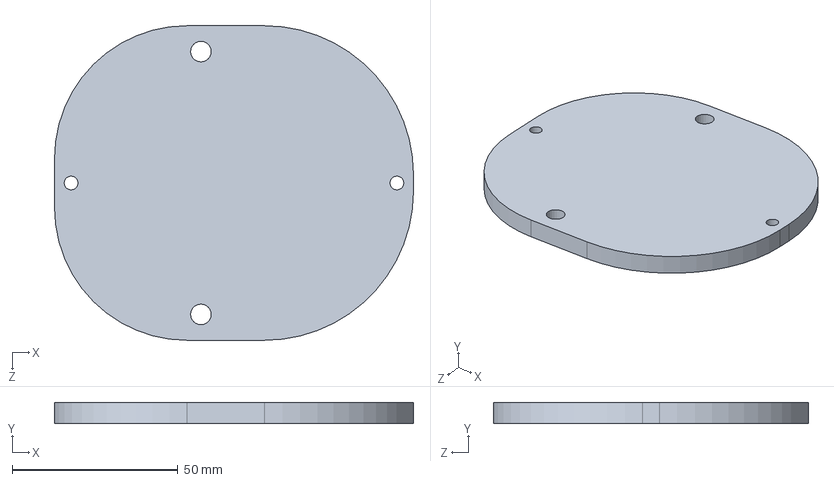
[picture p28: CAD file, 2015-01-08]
CAD/IMU mount/mount.SLDPRT
108.4 x 6.35 x 95.0 mm

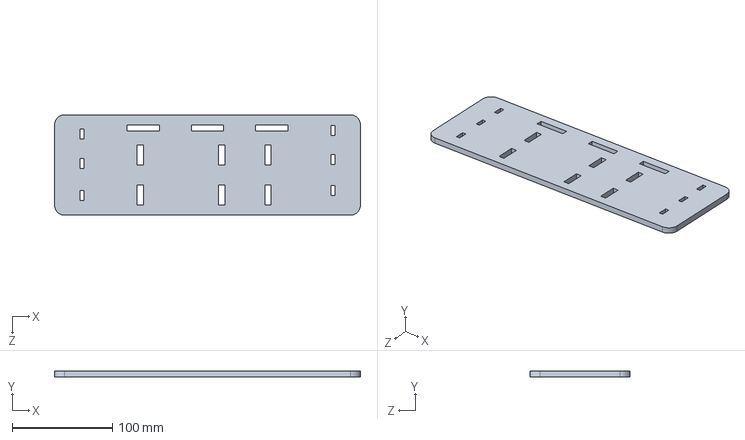
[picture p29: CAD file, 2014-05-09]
CAD/IMU tester mount/chestplate.SLDPRT
304.8 x 6.10 x 100.0 mm

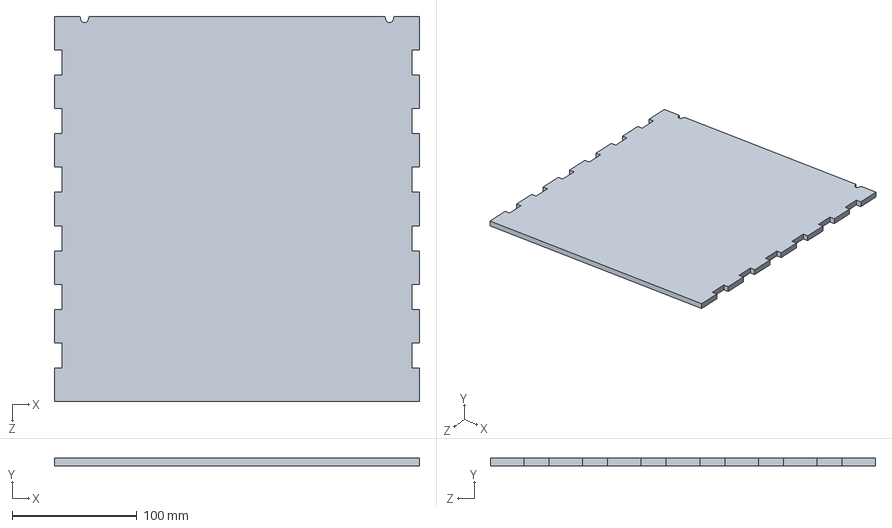
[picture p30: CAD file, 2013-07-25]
CAD/Pelican case/sunshield_back.SLDPRT
292.2 x 6.10 x 308.1 mm

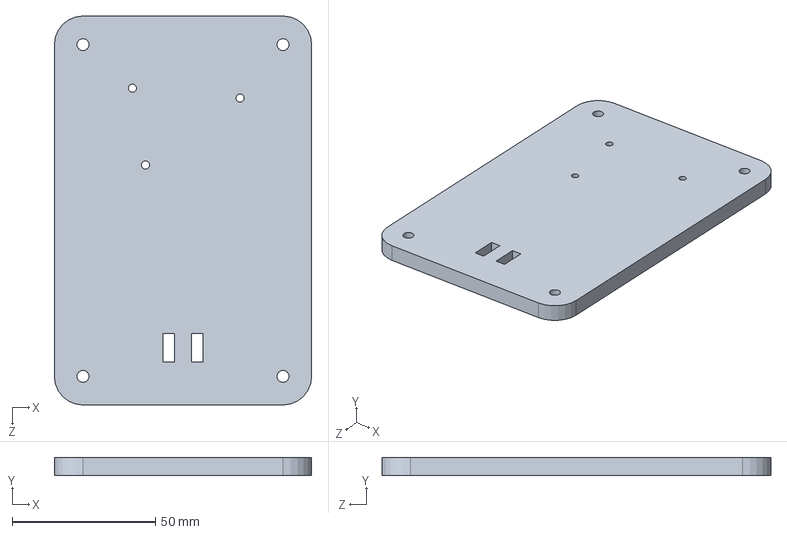
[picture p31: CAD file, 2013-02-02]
CAD/RC mount/RC mount.SLDPRT
89.8 x 6.35 x 135.8 mm

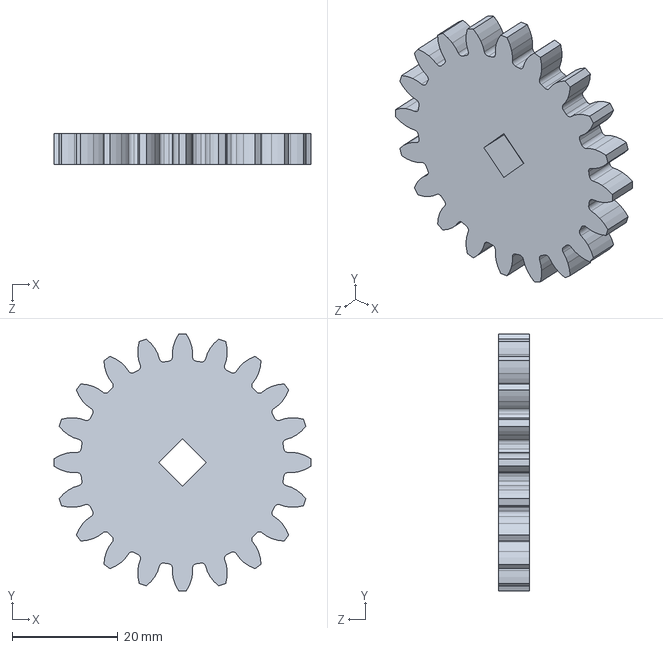
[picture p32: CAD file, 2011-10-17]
CAD/Rudder box/20 Gear.SLDPRT
48.7 x 48.7 x 5.84 mm

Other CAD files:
CAD/Rudder box/Assembly (Exploded).SLDASM
CAD/DSP-3000/mounting.SLDPRT
CAD/Rudder enclosure mountingboard/plate.SLDPRT
CAD/Rudder enclosure/mounting plate.SLDPRT
CAD/Charger Mount Plate/Mounting board.DXF
CAD/Charger Mount Plate/Mounting board.SLDDRW
CAD/Charger Mount Plate/Mounting board.SLDPRT
CAD/Charger Mount Plate/Mounting plank top.SLDPRT
CAD/Electronics Mountingboard/mountingboard.DXF
CAD/Electronics Mountingboard/mountingboard.SLDDRW
CAD/Groundstation mount/Backing_bottom.SLDPRT
CAD/Groundstation mount/Backing_top.SLDPRT
CAD/Groundstation mount/foam_surround.SLDPRT
CAD/Groundstation mount/mounting_board.SLDPRT
CAD/IMU tester mount/brace.SLDPRT
CAD/IMU tester mount/mounting board.SLDPRT
CAD/Pelican case/Pelican_Case_Plug.SLDPRT
CAD/Pelican case/Pelican_case_window.SLDPRT
CAD/Pelican case/sunshield_sidewall.SLDPRT
CAD/Rudder box/10 Gear.SLDPRT
CAD/Rudder box/30 Gear.SLDPRT
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

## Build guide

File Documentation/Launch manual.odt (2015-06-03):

SeaSlug Manual

June 3, 2015

# Launch Supplies Checklist

## Large black tub

(2x) 50ft of black rope Foot inflator, hose, and connector for the fender WD40 Wire brush | Shore power adapter Lifejacket Pillow 2 towels Extension cord (>50ft) Rubber & metal mallet

## Large red Stanford toolbox (electronics & tools)

Extra 8x AA batteries in their own sealed baggie DX5 RC Transmitter CANmodul USB<->CAN adapter & CANaconda USB/RS232 adapter Main & backup USB wireless controller Main & backup PICkit3 w/ USB & extension cable 2x walkie-talkies Multimeter XBee logic analyzer 5/16” nutdriver | Small red flathead screwdriver (for the ACS300 & IMU) Small Philips screwdriver (for the 2035) Big Philips (for the hatch screws/electrical terminals) Two small adjustable wrenches (for various nuts) Yellow wire strippers Small red pliers Headlamp Bag of screws (for the main hatch)

## Small red toolbox (cables/spare parts)

Female DB9<->3-pin CAN adapter RS232 adapter for the ACS300 board E-stop button Spare 0.1” signal connectors/jumpers (2-pin jumper, male-male, female-male) | Spare CANodes, 5V regulator, and shields (duplicate of everything onboard) in an anti-static bag Spare CAN parts/cables/connectors in a baggie Spare power parts/cables/connectors in a baggie

## Red backpack

My work laptop & power adapter Notebook & pen Food & water Cellphone & wallet Sunscreen | USB thumbdrive Extra pair of pants, warm sweatshirt/jacket This launch manual (printed in a 3-ring binder) Binoculars Hat and sunglasses

## Loose

- GPS/WSO100 stub mast
- Groundstation computer, all sealed up
- The mast (keep its 3 pipe clamps in the top of the large red toolbox)
- Black 10' fender

# Launching the boat (2 people)

## Part 1 - Prelaunch

1. Park the vehicle with trailer somewhere out of the way.
2. Remove the top hatch and store in the vehicle.
3. Secure and connect both the stub mast and the true mast.
4. Remove the black straps securing the SeaSlug to the trailer.
5. Secure the ropes, one to the front u-ring and one to the rear, using the two-half-hitches (https://en.wikipedia.org/wiki/Half_hitch) knot. Coil the remainder and leave readable from the very front of the bow.
6. The launcher driving the boat needs to change into shorts and shoes that can get wet.

## Part 2 – Launch

1. Partially (1/3) inflate the 3m black bumper and bring out to the dock and secure it in between two cleats using the black loop on one end and the green string on the other. Be sure to place it far enough from the ramp to fit a couple of boats. Also staying in the shade is nice.
2. Drive the vehicle up to the boat ramp and back it up.
3. Chock the trailer tires.
4. Disconnect the trailer hitch and pull forward >= 3m.
5. Remove the trailer hitch extension and secure it to the trailer.
6. Back the vehicle up and resecure the hitch.
7. Leave the 3rd wheel of the trailer down, but cranked all the way up.
8. Remove the trailer's wheel chocks.
9. Backup until the water reaches a few centimeters above the bottom of the U-bracket on the trailer.
10. Park the van and chock the front wheels.
11. The van driver gets out and disengages the front hook of the SeaSlug and throws both lines of rope to another person waiting on the dock.
12. The docker tows the SeaSlug over to where the bumper is and docks it snug against the dock (the boat will list slightly, but that is fine). Use a cleat-hitch (https://en.wikipedia.org/wiki/Cleat_(nautical)) to secure the fore and aft ropes snug, < 45o angle. Stow the ropes in nice coils near the cleats.
13. Get back in the vehicle, unchock the wheels, and reverse the trailer hitch process.

# Recovering the boat (2 people)

## Part 1 - Recovering

1. Leave the boat secured tight against the dock and turned off.
2. Using both people get the extended trailer onto the vehicle. Make sure the 3rd wheel is down but cranked all the way up.
3. Back the trailer into the water until the water covers the bottom of the u-bracket a few centimeters. This is fine if it's only during a tidal surge.
4. Have the docker undock the boat and move the boat forward until it sits a few meters behind the end of the trailer.
5. The docker should throw the forward rope to the launcher, who is waiting in the water on the front of the trailer. Once they have the rope, they should throw their aft rope onto the boat.
6. They guide the boat in straight to make sure the prop doesn't get damaged and untie the front line.
7. Then the front crank hook is attached and the boat is ranked up and the forward eyemount is seated up above the pulley for the crank hook ribbon.
8. Now the launcher can tow the boat out of the water. The hitch must be switched back to the main trailer hitch before pulling all the way out of the launch ramp.

## Part 2 – Securing

1. Retrieve all supplies from the boat and the dock and secure them in their containers in the vehicle.
2. Strap down the sides of the SeaSlug to the trailer with the black cinch ropes.
3. Secure the internal electronics compartment.
4. Secure all hatches (main hatch with at least 3 screws).
5. Disconnect the stubmast and rear rope.

# Storing the SeaSlug

## For transport

- Main electronics hatch is secured.
- Battery tray is lashed down.
- All exterior hatches are secured (main hatch has 3 or more screws holding it down).
- Mast mounting hole is covered.
- Black straps are securing the sides of the boat to the trailer.
- The rudder is at 0 degrees.
- The trailer hitch extension is secured through its middle hole.
- The NMEA2000 connector on the rudder hatch is sealed.
- All internal power is off: bilge, electronics, and actuators.

## For storage on land (post-launch)

- Propeller has been rinsed out with water through the internal hose connection and run for at least a minute.
- Sides and bottom of the hull has been rinsed off.
- The hitch rests on a stand.
- The front wheel is down just above the ground in case the hitch stand fails.
- The hitch latch is bolted or secured back so that it's non-trivial for some random stranger to hitch it up and steal it.
- The top hatches are all secured (main hatch has 3 or more screws holding it down).
- The NMEA2000 connector on the rudder hatch is sealed.
- The bilge pump power is on.
- The electronics and actuator power is off.

# Final Testing Checklist

This should be done a day or two before the launch and then the SeaSlug should remain undisturbed until launch day.

Groundstation | In sealed enclosure w/ radio connection Receives telemetry from all systems (test w/ all real sensors and in HIL) Retrieves/modifies waypoints Retrieves/modifies parameters (esp. disabling autonomous mode)
Primary controller | Rudder calibration Rudder control Switching modes Throttle
Secondary controller | Transmitter calibration Rudder calibration Rudder control Throttle control Overrides primary controller when on Can be on but disabled without controlling anything
Autonomous control | Runs a complete waypoint set in Full-HIL. Be sure to connect the hose when doing this out-of-water!
Datalogger | Receiving telemetry. Test with a groundstation connection to the output port as well as a watching the LED indicators on it. Validated data recorded during the run with mavloss and mavsummarize tools from PyMAVLink.
Return-to-base functionality | Triggered when pulling the e-stop Triggered when the rudder node disconnects for >= 1.25s Triggered when the IMU disconnects for >= 1.25s Triggered when the DST800 disconnects for >= 1.25s Triggered when the groundstation disconnects for >= 30s Triggered when the GPS cuts out for >= 10s

# Prep for Launch (>= 1 day before)

- The Final Testing Checklist has been gone through and all systems are operational.
- Vessel has been fully charged so the charger shows solid green for all 4 battery banks.
- GCS has been fully charged.
- Development laptop has been fully charged.
- Cameras fully charged (GoPro, cameras, etc.).
- Old convertible tablet has been fully charged.

# Preflight checklist

- Stub mast secured with sensors connected
- Rudder hatch secured
- Main mast secured
- Front IMU hatch secured
- Electronics hatch secured
- Battery ballast tray secured
- Rudder calibrated
- Primary controller check (full rudder/throttle range, autonomous mode switching, can calibrate)
- Emergency controller check (full rudder/throttle range, autonomous mode switching, can calibrate)
- GPS status check (see in groundstation)
- Supplies onboard: RC transmitter (waterproof), primary controller (waterproof), groundstation (waterproof), spare batteries (waterproof), cellphone (waterproof), radio (waterproof)
- Lifejacket on
- Actuator and electronics batteries on
- Groundstation operational and receiving telemetry at correct rates
- Electronics are all secured inside the SeaSlug
- Fore and after ropes coiled and within reach
- E-stop disengaged
- The IMU readings in QGC look stable and correct

# Operating Guide

Operating the vessel can be broken down into three main modes of operation: manual control, autonomous control, and emergency manual control. Further details on each mode is given below.

## Manual Control

Manual control is done through the QGroundControl (https://github.com/mavlink/qgroundcontrol) program. It can communicate with joysticks, gamepads, and other controllers to control any vehicle it connects to. While the SeaSlug uses some custom messages to output telemetry, the bulk of the interaction with the vehicle uses the common messageset which is always available in QGC.

To enable manual control, simply connect a suitable PC controller over USB, open Settings and map the throttle and yaw values to the desired axes. Note that L1 on the Logitech F710 controller is used to enable setting the throttle value, so if that's not held down when moving the throttle axis, nothing will happen. Additionally, button 8 is hard-coded to activate the rudder calibration regardless of controller. Both of these were done so as to support QGC out-of-the-box.

## Autonomous Control

Autonomous control can be enabled through the QGroundControl groundstation computer. It can either be enabled by setting the AutoMode parameter. The controller can also be used to toggle the state of the vehicle by mapping the Toggle Autonomy action to a button on it. This is the preferred method and it guarantees that manual control can be switched to in case of problems with the autonomous controller.

QGroundControl provides methods for changing onboard parameters, managing waypoints, and visualizing data. Most of the built-in features are supported with the SeaSlug, and the user should be referred to the QGC documentation.

## Emergency Control

In an emergency, where the vessel is out of control or needs to be restrained for some other reason, the simplest thing to do is hit the e-stop button located to the rear of the vessel. This will disable the propeller motor controller and all systems will be held in reset. This should also center the rudder, making towing the vessel easy if it's required.

In a non-emergency situation or one in which direct control of the vehicle is desired, the backup/secondary/emergency controller can be used. It has its own CANode so that it can talk directly to the rudder and propeller controllers and bypass the primary controller completely. When this happens, the PrimaryNode goes into reset. This allows the boat to also be controlled in situations where the PrimaryNode is not responding, which is very useful for testing purposes.

The emergency controller is a Spektrum Dx5 RC transmitter with a receiver mounted inside the vessel. The range should be good out to at least 50m. It should be labeled, but the main controls are:

- Left-stick, up/down controls the throttle
- Left-stick, left/right controls the rudder angle
- Switch 1 is an enable, when this is active this controller has control of the vessel. If you are concerned about a situation it is advised to keep this controller on and disabled. Flicking this switch can provided faster vehicle response than going through the primary controller.
- The right-analog stick can be used to toggle the rudder calibration. A left-right-left motion will toggle calibration.

## Error Conditions

There are various error conditions that can be triggered onboard the vessel. The Primary Node shows most of them in its Reset bitfield. There are, however, some situations that should be described here as they require operator intervention.

### E-stop

This is triggered by the ACS300 motor driver board not transmitting on the CAN bus. This can be the result of the e-stop being triggered, the ACS300 not being powered, or the ACS300 not being connected to the CAN bus. All of these conditions should be checked if the error should not currently exist.

### Rudder motor stall

There have been issues in previous launches where the rudder motor actually went the wrong direction while the motor driver board was failing and then it stopped moving at all. To prevent overheating and for the protection of the vessel, code was added to detect for these conditions. These result in a rudder error which propagates into a primary node error. This can also trigger on startup or if the rudder is moved by an external force. This error can be cleared by re-calibrating the rudder. Recalibration does not use this motor stall checking code so if there is still something wrong with the rudder during calibration, it's on the operator to sort it out.

### Return-to-base

This is triggered by a variety of error conditions when the vessel is under autonomous control. If any of these errors are present, they'll also prevent the vehicle from being switched into autonomous control. Once RTB is triggered, it cannot be cleared by anything short of manual intervention (by design). To clear this error state switch the vehicle to manual control, which will clear the error immediately. Right now the following errors trigger this mode:

- Ground station disconnected for >= 30s
- GPS disconnected, or giving bad readings, for >= 1.25s
- DST800 disconnected for >= 1.25s
- IMU disconnected for >= 1.25s
- Rudder disconnected for >= 1.25s
- The e-stop being activated or the ACS300 disconnecting
- The rudder node having any errors

# Simulation

Simulation is split up into three sections: full software simulation, half hardware-in-the-loop, full hardware-in-the-loop. These simulators are all contained within the basic_model folder. The simulation_constants.m file is also here, which sets some basic state data for the vehicle at the start of simulation. And the controller itself is located in the primary_node folder.

## Full Software Simulation

The full simulation environment is contained within the Full_sim.mdl file. It is merely scaffolding supporting the connection of the Plant.mdl implementing the environment & vessel simulation with the controller.mdl. Running this model will generate output data similar to what's recorded during an actual boat launch. The Full_sim*.m files are visualization aids for viewing the results of the simulation. Further investigation can be done manually.

## Half HIL

Hardware in the loop simulation is first done with just the controller moved onto the real hardware. There are no connections from the controller to real actuators or sensors at this point. Testing this is done by using the HILNode to translate the UDP connection from Simulink to the CAN bus messages that the PrimaryNode works on. Note that in this mode the controller has no idea that it is running in simulation. This means that the exact same procedure to run & operate the SeaSlug applies here!

The HILNode needs to be programmed, powered on, and connected over Ethernet to the simulation computer. It also needs a CAN connection to the PrimaryNode, which is also powered on. The groundstation, along with the primary controller, is also required at this stage and should be connected over serial or radio. Note that this CAN connection needs to be a proper bus with the two 120Ω resistors for this connection to work. With the system connected as so, running the HIL_sim.mdl file will run the Plant onboard the simulator computer and leave the controller to process the data offboard. The HILNode has been programmed to use the same transmission rates as used by the actual hardware sensors.

Note that for HIL to work properly, the GPS, IMU, and DST800 cannot also be transmitting on the bus. There are reset flags for each of those peripherals, so check the NODE_STATUS message in QGroundControl. See the HilNode.h file for details on what each flag. If any of those flags are active the red LED will be lit as well.

To initiate HIL, start the HIL simulation model. At this point the amber LED on the HILNode should be blinking at twice its normal rate. The controller's GPS LED should also go green as it's receiving good GPS data from the simulator. And finally, on the simulator side it can be checked by looking in /HIL Interface at the latency display at the bottom (this should be very low single digits for the simulation results to be good).

Now to actually begin the simulation, load the desired mission waypoints, set the throttle, and switch to autonomous mode using QGroundControl.

## Full HIL

Full HIL differs from Half HIL only in the connection of the PrimaryNode to the actuators. This can be done onboard the vessel or in a controlled lab setting with a rudder and propeller model. The HILNode detects the data transmit by the rudder node and the ACS300 automatically, so no changes to the PrimaryNode, HILNode, or simulator need to be made in the transition to Full HIL. With the addition of the actuators be sure to run through any necessary calibration procedures as well.

## Additional simulators

The above three simulations are all that is required for testing the vehicle and prepping for another launch. The following simulators add additional debugging and testing capabilities that are not directly required for a launch but can be helpful.

These simulators all rely on real data from actual launches. Depending on the dataset the initialization routines they use (*_sim_init.m) may require modification. The data is chosen based on a CSV file produced from a MAVLink datastream that has all the required messages and the number of the autonomous run contained within that recording. These are easy to find using the static_plots.m script provided in the /Code/Libs/MATLAB folder. And further analysis of a particular autonomous run can be done with the dynamic_plots.m script.

### Plant_sim.mdl

This file implements a simulator for testing the Plant in open-loop on real data from an autonomous section of a real boat launch. The goal of this simulator would be for the Plant and the actual recorded data to be identical. Running this model prompts the user for a file and an autonomous run section to analyze. The results can be displayed and analyzed with the Plant_sim_visualize.m script.

### Replay_sim.mdl

To test new controller modifications, the Replay simulator can be used. It is easy to make modifications to the controller and test them in simulation on real data. Running this model works similarly to the Plant simulator: the user is prompted for a CSV file and an autonomous run number.

Note that this model doesn't use a model reference for the controller block, because it needs access to data within the model and Simulink prevents that. This means that changes done to this model or the controller need to be manually copied to the other.

# SeaSlug Resources

## Physical

- The BotCave contains a variety of non-necessary and weatherproof components.
- Under the drill presses in lab are boxes containing various components.
- The main mast resides in the corner of the lab
- Above the cabinets are tubs and additional supplies.
- The SeaSlug and its trailer are located behind E2, by the woodshop at the fire road entrance. GPS 37.001751,-122.062113

## Code & Data

- The main code repository for the SeaSlug is: https://github.com/Susurrus/Autoboat
- A Simulink library used in the Autoboat repo is: https://github.com/Susurrus/MicroSimulink-Library
- Additional data is stored on the Byron server at /data/projects/SeaSlug/
- The wiki has pictures and reference material: http://byron.soe.ucsc.edu/wiki/autoboat/
- The CANode and its associated hardware are in a repo on Byron as well: ASL_eCAD.git
- QGroundControl is at https://github.com/mavlink/qgroundcontrol.
- MAVLink is at https://github.com/mavlink/mavlink (https://github.com/mavlink/https://github.com/mavlink/mavlink). This isn't necessary to download, as the generated files are stored in the Autoboat repository.
- The datalogger code is at: https://github.com/Susurrus/SLUGS-Logger
- Current code for the Tokimec IMU is at: https://github.com/Susurrus/tokimec
- Potential future IMU code is at: https://github.com/FrauBluher/MPU60xx
- A now-unused serial/UDP software bridge exists at: https://github.com/Susurrus/serial2udp
- The repository for the CANaconda USB-CAN adapter is at: https://github.com/xela144/CANaconda
- The repository for Bryant's Ph.D. dissertation on the SeaSlug is at: https://github.com/bwmairs/dissertation

# Driving Directions

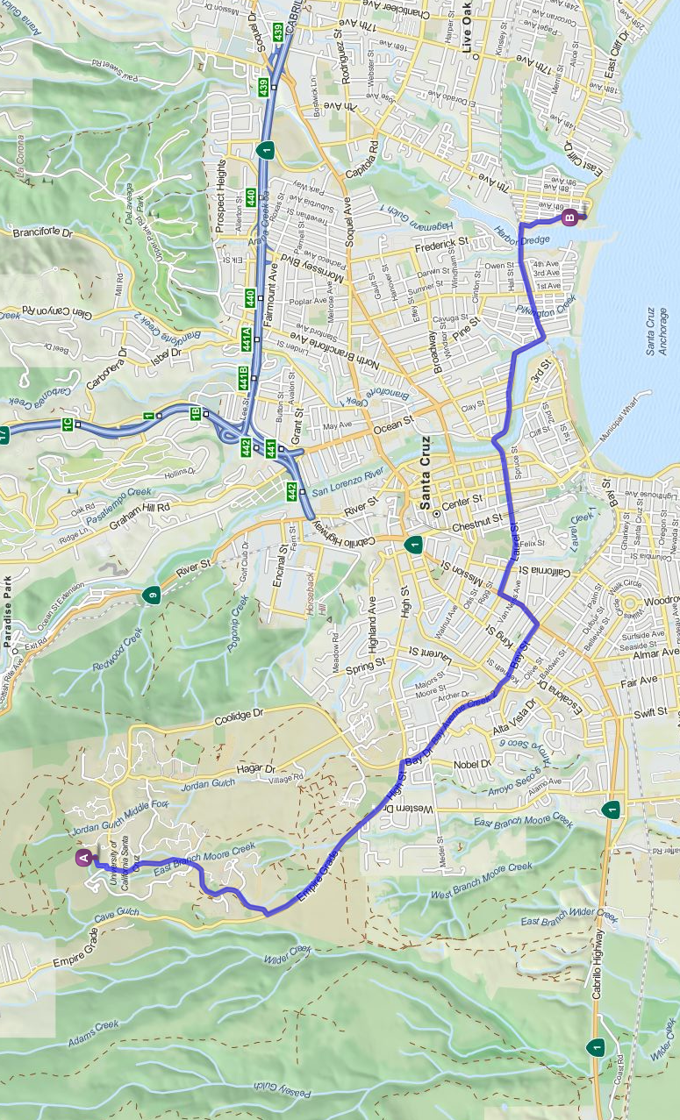
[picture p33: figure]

# The Groundstation Computer System (GCS)

  - QGroundControl can be started from the shortcut on the taskbar, which is a shortcut to the release build of QGC.
  - No data should be permanently stored on the groundstation. It should be assumed that it can be reformatted at any time. So all data should be backed up immediately upon returning from a launch.
  - The default user is 'asl'. There is no password and they have administrator rights.
  - Other useful tools installed are Git and Saleae's Logic.
  - All code is stored in ~/Projects.
  - The computer needs a connection to the Logitech F710 controller and the 3DR radios for controlling the SeaSlug and require the black 4-port USB hub.
  - All GCS parts are sealed in a heavy-duty plastic bag for weatherproofing during launches. This bag then velcros into the blue chassis.
  - When launching the power setting should be set to Balanced. This turns the screen brightness all the way up, prevents it from sleeping, but turns off the screen after 2 minutes.
  - Since the GCS is sealed it is prone to overheating leave covered when not in use.
  - QGroundControl has been compiled with audio output, so either a Bluetooth headset, headphones, or the built-in speakers can be used with it.
  - The power button does not do anything when the computer is on, it's been disabled. It does, however, turn it on.
  - The touch screen has been disabled as the expected input method is through a Wacom-compatible pen.

# Using QGroundControl

- These instructions assume you have built QGC with the “seaslug” messageset as defined within the Autoboat repository and the audio interface. All other optional components should be disabled (for performance and compilation speed reasons).
- To connect to the SeaSlug have a wired or wireless serial connection to the main GCS datastream. The datalogger stream will still register in QGC, but it's only telemetry output.
- Make sure the Logitech F710 controller is connected. Insert the controller's USB transceiver and press the center silver Logitech button to start the connection process. The LED should blink briefly and then go solid. Once the gamepad is connected pressing the bottom-left “Mode” button will toggle the LED next to it on and then off (leave it off).
- Open QGroundControl and enable manual control of the SeaSlug by going to File→Settings→Joystick and enabling it. If the gamepad doesn't appear, repeat the above directions. Configure the joystick so that: the up-down motion of the left thumbstick is inverted throttle, the left-right motion of the left thumbstick is inverted yaw, and Button 9 is set to “Toggle Autonomy”. The rudder calibration button is not a QGC mapping, but is hard-coded into the SeaSlug controller.
- If this is the first time running QGroundControl, press the “Connect” button in the upper right to open the Connections Manager. Create a new serial connection on the proper port at 115200baud and hit “Connect.”
- If the serial connection already exists, hit “Connect”.
- MAV20 should appear, which is the SeaSlug.
- When finished with QGC, closing the program or hitting the “Disconnect” button will open a dialog prompting you to save the log file. The default location is ~/Documents/QgroundControl/FlightData.

# Processing recorded MAVLink data

The process for extracting data relies on the tools within the MAVLink project and Python. While MAVLink is partially compatible with Python3, sometimes there are issues so Python2.7 is recommended. It should be downloaded and exist on the $PYTHONPATH. Additionally the seaslug.xml message definition file from the Autoboat repository should exist in the $MAVLINK_DIR/message_definitions/v1.0/ directory. With that set up all MAVLink scripts can be run like:

python -m pymavlink.tools.*

## Extracting groundstation data

1. QGroundControl saves recorded MAVLink data with 64-bit Unix timestamps embedded in it which is how the following PyMAVLink tools extract time information.
2. Extracting a CSV file can be done with PyMAVLink's mavlogdump tool:  python -m pymavlink.tools.mavlogdump --dialect=seaslug --format=csv --types=COMMA,SEPARATED,LIST,OF,MESSAGES LOG_FILENAME.mavlink > LOG_FILENAME.csv
3. This CSV file can then be imported into MATLAB using the ProcessCsvFile MATLAB function provided in the Autoboat repository at /Code/Libs/MATLAB/. Like:  data = ProcessCsvFile('LOG_FILENAME.csv');
4. Note that when this CSV file is imported, it'll have NaNs when the message didn't have data. These can be easily filtered with MATLAB's isnan function.

## Extracting datalogger data

5. Run the Python script from the SLUGS-Logger project's Testing/extractData.py script, giving it the XXXX.log file recorded from the datalogger. This will create a XXXX_extracted.log file. Rename it to XXXX.mavlink for clarity. It may spit out some errors, but those are common because of how the datalogger generates file and can almost always be safely ignored.
6. Follow the instructions for extracting data from the groundstation datastream except add the --no-timestamps argument to the call to mavlogdump, because the datalogger doesn't inject timestamps into its recorded datastream.

## Additional tools

Once data is in a CSV format, see the MATLAB functions available in the Autoboat repository at: /Code/Libs/MATLAB/ and /Code/Scripts/MATLAB/.

For working with data still in MAVLink format, see the various tools offered in the MAVLink repository's pymavlink library at /pymavlink/tools/. Especially useful are mavloss and mavsummarize.

# Node status/error bits and LEDs

## Primary node

LEDs
Amber | Blinks at 1Hz
Red | System is in a reset state. See the Error bits below.
GPS | Solid when there is a good GPS connection. Blinks at 4Hz when no good GPS data is being received. Nothing when the GPS is disconnected.
Auto | Solid when the system is in autonomous mode. Blinking at 4Hz when in autonomous mode and overridden by the backup manual controller.

Status bits | | Error bits
0x0001 | Vehicle is under autonomous control. | 0x0001 | Active during the first 5 seconds of bootup.
0x0002 | System is in return-to-base mode. | 0x0002 | The groundcontrol station has been disconnected for >= 30s.
0x0004 | ECAN peripheral in the transmission error state. | 0x0004 | The GPS unit has had a bad fix for >= 10s.
0x0008 | ECAN peripheral in the reception error state. | 0x0008 | The DST800 water speed sensor is disconnected
0x0010 | The GPS is no longer giving good readings | 0x0010 | Manual override has been engaged by the secondary controller.
0x0020 | The RC node is missing from the CAN bus. | 0x0020 | The rudder is undergoing calibration.
| | 0x0040 | The rudder is uncalibrated.
| | 0x0080 | The system is in emergency-stop mode, actuators are centered and stopped, system will not respond to any commands; it's dead in the water. This can also occur if the CAN connection to the ACS300 is lost/unavailable.
| | 0x0100 | The IMU is disconnected.
| | 0x0200 | The rudder is disconnected.
| | 0x0400 | Return-to-base mode has been engaged due to an error condition.
| | 0x0800 | The rudder is in an error state

## RC node

LEDs
Amber | Blinks at 1Hz normally. Double-blinks at 1Hz when the transmitter is connected.
Red | System is in a reset state OR a fatal error has occurred. See the Error bits below.
Transmitter | Solid when the RC transmitter is on and connected.

Status bits | | Error bits
0x0001 | The RC transmitter is connected and in manual control mode | 0x0001 | The ACS300 is not detected or the e-stop is active.
0x0002 | The RC transmitter is connected | 0x0002 | The RC node is uncalibrated.
| | 0x0004 | ECAN peripheral in the transmission error state.
| | 0x0008 | ECAN peripheral in the reception error state.

## Rudder node

LEDs
Amber | Blinks at 10Hz while uncalibrated. Blinks at 4Hz while calibrating. Blinks at 1Hz once calibrated.
Red | A fatal error has occurred.

Status bits | | Error bits
0x0001 | Rudder is calibrated. | 0x0001 | Motor is inoperable
0x0002 | System is calibrating. | 0x0002 | E-stop is active
0x0004 | The starboard limit is being triggered.
0x0008 | The port limit is being triggered.

## IMU node

LEDs
Amber | Blinks at 1Hz normally. Blinks at 2Hz when the IMU is connected and messages are being successfully decoded.
Red

Status bits | | Error bits
0x0001 | The IMU is actively transmitting.

# People of Interest

Rusty Kingon
Contact for reserving the chase boat. Coordinator for the boating program. Let him know ~1 week before a boat is needed to get one reserved. | Email: rlkingon@ucsc.edu Cell: 831-261-7126 Office: 831-425-1164 Location: FF dock, Santa Cruz Harbor
Dustin Smucker
Contact for reserving a van. Associate Direction of Recreation at OPERS. | Email: dsmucker@ucsc.edu Office: 831-459-2668 Location: OPERS recreation office
Christa Mercado
In charge of vehicle registration for the boat and the trailer (aka DMV stuff). Inventory Equipment Assistant. | Email: cnmercad@ucsc.edu Phone: 831-459-2228
Janean Mariani
In charge of asset management of the boat and the trailer. Fleet Coordinator at UCSC Fleet Services. | Email: mariani@ucsc.edu Phone: 831-459-2355

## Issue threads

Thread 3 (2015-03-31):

IMU node doesn't report temperature

Susurrus, 2015-03-31:

Susurrus, 2015-06-03:
Also fixed by fixing #11.

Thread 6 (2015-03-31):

Replace rudder motor driver board

Susurrus, 2015-03-31:
The one we're using burns too much power as heat and will eventually cause overheating problems. It should be replaced with a better version. Replacement should still be able to do 2A driving, 1A idle current.

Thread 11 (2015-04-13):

Replace the Tokimec sensor

Susurrus, 2015-04-13:
Use something cheaper and better documented, like the YEI 3-Space Sensor.

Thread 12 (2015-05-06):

Remove Lubin's blockset from the RC node

Susurrus, 2015-05-06:

Susurrus, 2015-06-03:
Just missing an IC driver to do this.

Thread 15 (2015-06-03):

Clamp the water speed and global speeds to >=1.0

Susurrus, 2015-06-03:
This should prevent really bad performance when going at low speeds. Just need a simple `max(v_w, 1.0)` and `max(v_g, 1.0` term in the code that converts from acceleration command to rudder angle.

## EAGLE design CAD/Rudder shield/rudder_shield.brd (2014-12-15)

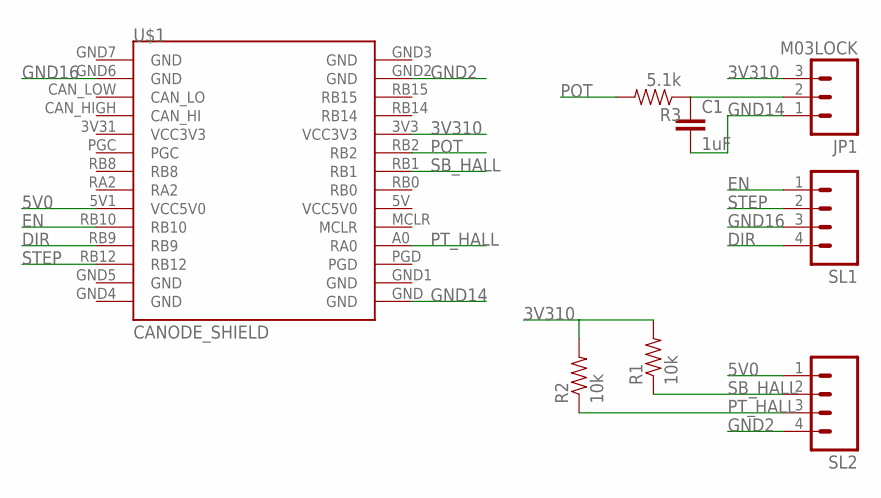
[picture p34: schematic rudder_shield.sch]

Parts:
C1: 1uF; 1206
JP1: M03LOCK; 1X03_LOCK
R1, R2: 10k; 0805
R3: 5.1k; 0805
SL1, SL2: M04LOCK; 1X04_LOCK
U$1: CANODE_SHIELD

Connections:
3V310: JP1.3, R1.2, R2.2, U$1.3V3 (VCC3V3)
5V0: SL2.1, U$1.5V1 (VCC5V0)
DIR: SL1.4, U$1.RB9
EN: SL1.1, U$1.RB10
GND2: SL2.4, U$1.GND2 (GND)
GND14: C1.2, JP1.1, U$1.GND
GND16: SL1.3, U$1.GND6 (GND)
unnamed: C1.1, JP1.2, R3.1
POT: R3.2, U$1.RB2
PT_HALL: R2.1, SL2.3, U$1.A0 (RA0)
SB_HALL: R1.1, SL2.2, U$1.RB1
STEP: SL1.2, U$1.RB12

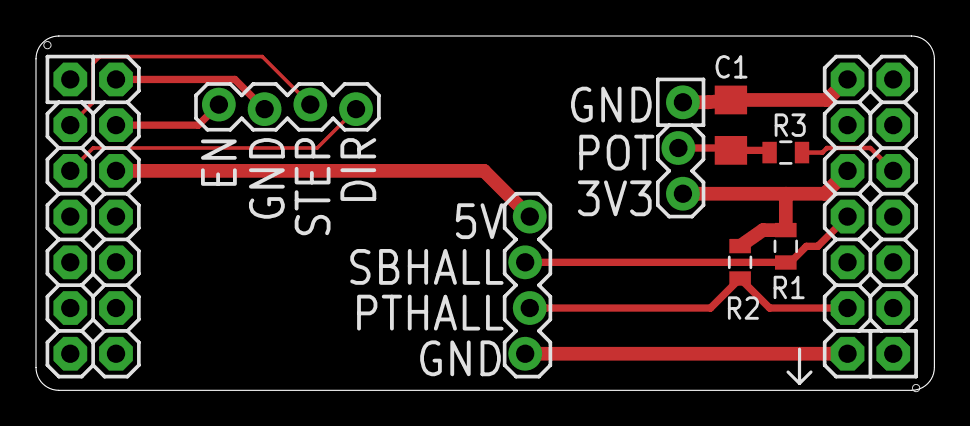
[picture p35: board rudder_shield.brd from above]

Board: 2 copper layers, 49.9 x 19.7 mm, 8 parts (0 on the bottom side), 12 nets.

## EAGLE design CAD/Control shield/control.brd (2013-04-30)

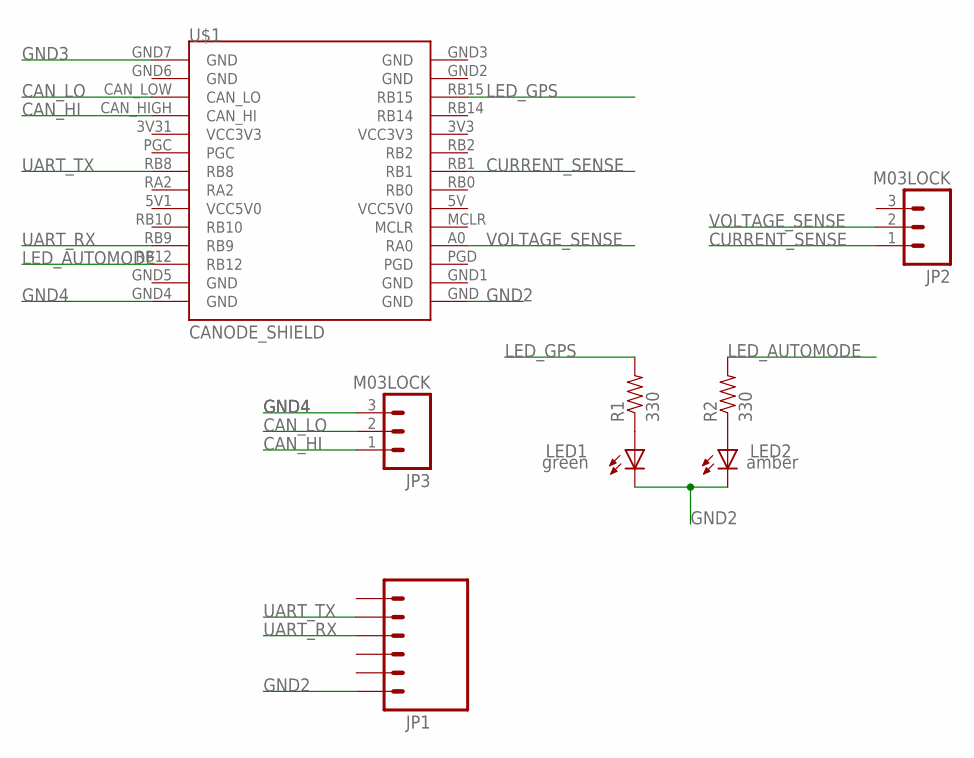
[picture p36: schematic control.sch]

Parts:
JP1: M06LOCK; 1X06_LOCK
JP2, JP3: M03LOCK; 1X03_LOCK
LED1, LED2: LED1206; LED-1206
R1, R2: 330; 0805
U$1: CANODE_SHIELD

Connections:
CAN_HI: JP3.1, U$1.CAN_HIGH (CAN_HI)
CAN_LO: JP3.2, U$1.CAN_LOW (CAN_LO)
CURRENT_SENSE: JP2.1, U$1.RB1
GND2: JP1.1, LED1.C, LED2.C, U$1.GND
GND3: U$1.GND7 (GND)
GND4: JP3.3, U$1.GND4 (GND)
LED_AUTOMODE: R2.2, U$1.RB12
LED_GPS: R1.2, U$1.RB15
unnamed: LED1.A, R1.1
unnamed: LED2.A, R2.1
UART_RX: JP1.4, U$1.RB9
UART_TX: JP1.5, U$1.RB8
VOLTAGE_SENSE: JP2.2, U$1.A0 (RA0)

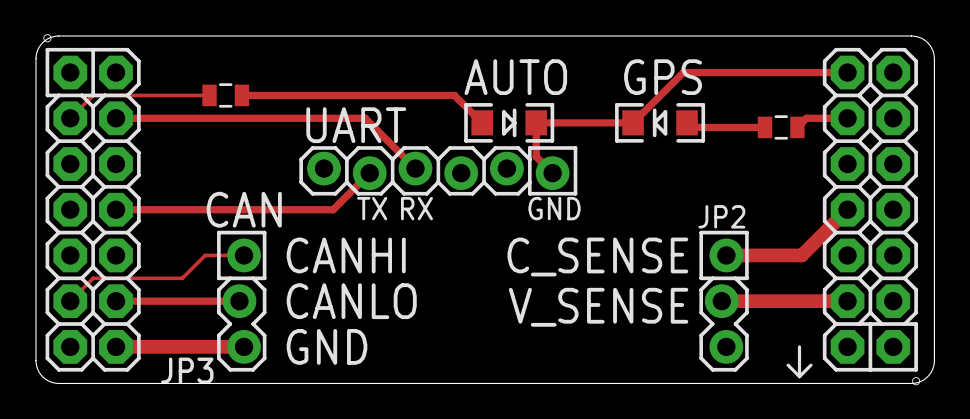
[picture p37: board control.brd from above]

Board: 2 copper layers, 49.9 x 19.3 mm, 8 parts (0 on the bottom side), 12 nets.

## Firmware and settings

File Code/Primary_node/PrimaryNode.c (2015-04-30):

// C standard library includes
#include <stdlib.h>
#include <stdio.h>

// Microchip standard library includes
#include <xc.h>
#include <pps.h>
#include <adc.h>
#include <uart.h>
#include <dma.h>
#include <timer.h>

// Project includes
#include "Node.h"
#include "MavlinkGlue.h"
#include "Acs300.h"
#include "Uart1.h"
#include "Uart2.h"
#include "Ecan1.h"
#include "PrimaryNode.h"
#include "DataStore.h"
#include "EcanSensors.h"
#include "Rudder.h"
#include "Actuators.h"
#include "MissionManager.h"
#include "Conversions.h"

// MATLAB-generate code includes
#include "controller.h"

// Define some macros for setting pins as inputs or outputs using the TRIS pins.
#define OUTPUT 0
#define INPUT 1

// Declare some macros for helping setting bit values
#define ON  1
#define OFF 0

// Specify how long after startup the node should stay in reset to let things stabilize. Units are
// centiseconds.
#define STARTUP_RESET_TIME 200

// Keep track of the processor's operating frequency.
#define F_OSC 80000000L

// Calculate the BRG register value necessary for 115200 baud with a 80MHz clock.
#define BAUD115200_BRG_REG 21

// Define the maximum value of the ADC input
#define ANmax 4095.0f

// Set the limit for when the GCS is considered disconnected at 30s. This leaves enough time for the
// chase boat to respond to when the first disconnection notice is received to prevent the SeaSlug
// from going into RTB mode.
#define GCS_DISCONNECTION_TIME 3000

// The time limit (in units of 0.01s) before a GPS disconnection state becomes an unrecoverable
// error.
#define GPS_DISCONNECTION_TIME 1000

// Store analog sensor data here

static struct {
    float powerRailVoltage;
    float powerRailCurrent;
} analogSensors;

// The trigger limit for when a STATUS_TEXT message should be sent with the current system status.
// Currently it's every 30s (so in units of 0.01s) after a waypoint has been hit. Additionally, this
// should trigger when switching to autonomous mode.
#define SAY_STATUS_COUNTER_LIMIT 3000
uint16_t sayStatusCounter = 0;

// This is used to store sensor availability from the last sample time in order to trigger on
// sensor availability changes.

static struct {
    bool gpsEnabled;
    bool gpsActive;
    bool imuEnabled;
    bool imuActive;
    bool wso100Enabled;
    bool wso100Active;
    bool dst800Enabled;
    bool dst800Active;
    bool powerEnabled;
    bool powerActive;
    bool propEnabled;
    bool propActive;
    bool rudderEnabled;
    bool rudderActive;
    bool rcNodeEnabled;
    bool rcNodeActive;
    bool gyroEnabled;
    bool gyroActive;
} lastSensorAvailability;

// Store actuator commmands here. Used by the MAVLink code.
ActuatorCommands currentCommands;

// Set up DMA memory for the ADC. But with the scatter- gather mode enabled on the ADC, we reserve
// an array for all 16 possible inputs, so we align to 32-byte boundaries instead.
#ifdef __dsPIC33FJ128MC802__
static volatile uint16_t adcDmaBuffer[16] __attribute__((space(dma), aligned(32)));
#elif __dsPIC33EP256MC502__
static volatile uint16_t adcDmaBuffer[16] __attribute__((aligned(32)));
#endif

// Declare some function prototypes.
void Adc1Init(void);
void PrimaryNode100HzLoop(void);
void PrimaryNodeMuxAndOutputControllerCommands(float rudderCommand, int16_t throttleCommand, bool forceTransmission);
void SetStatusModeLed(void);
void SetAutoModeLed(void);
void SetResetModeLed(void);
void SetGpsLed(void);
void TransmitNodeStatus2Hz(void);
float ProcessManualRudderCommand(float rc);
int16_t ProcessManualThrottleCommand(int16_t tc);
void ClearStateWhenErrors(void);
void SendAudioStatusUpdate(void);
void TransmitChannelUsage(void);

// Set processor configuration settings
#ifdef __dsPIC33FJ128MC802__
// Use internal RC to start; we then switch to PLL'd iRC.
_FOSCSEL(FNOSC_FRC & IESO_OFF);
// Clock Pragmas
_FOSC(FCKSM_CSECMD & OSCIOFNC_ON & POSCMD_NONE);
// Disable watchdog timer
_FWDT(FWDTEN_OFF);
// Disable JTAG and specify port 3 for ICD pins.
_FICD(JTAGEN_OFF & ICS_PGD3);
#elif __dsPIC33EP256MC502__
// Use internal RC to start; we then switch to PLL'd iRC.
_FOSCSEL(FNOSC_FRC & IESO_OFF);
// Clock Pragmas
_FOSC(FCKSM_CSECMD & OSCIOFNC_ON & POSCMD_NONE);
// Disable watchdog timer
_FWDT(FWDTEN_OFF);
// Disable JTAG and specify port 2 for ICD pins.
_FICD(JTAGEN_OFF & ICS_PGD2);
#endif

int main(void)
{
    /// First step is to move over to the FRC w/ PLL clock from the default FRC clock.
    // Set the clock to 79.84MHz
    PLLFBDbits.PLLDIV = 63; // M = 65
    CLKDIVbits.PLLPOST = 0; // N2 = 2
    CLKDIVbits.PLLPRE = 1; // N1 = 3
    // Set the clock to 140MHz (Kept for possible future use)
//    PLLFBDbits.PLLDIV = 74; // M = 76
//    CLKDIVbits.PLLPOST = 0; // N2 = 2
//    CLKDIVbits.PLLPRE = 0; // N1 = 2

    // Initiate Clock Switch to FRM oscillator with PLL.
    __builtin_write_OSCCONH(0x01);
    __builtin_write_OSCCONL(OSCCON | 0x01);

    // Wait for Clock switch to occur.
    while (OSCCONbits.COSC != 1);

    // And finally wait for the PLL to lock.
    while (OSCCONbits.LOCK != 1);

    // Set the ID for the primary node.
    nodeId = CAN_NODE_PRIMARY_CONTROLLER;

    // We aren't calculating CPU load for the primary controller
    nodeCpuLoad = UINT8_MAX;

    // Initialize UART1 to 115200 for groundstation communications.
    Uart1Init(BAUD115200_BRG_REG);

    // Initialize UART2 to 115200 for datalogger recording.
    Uart2Init(BAUD115200_BRG_REG);

    // Initialize the EEPROM for non-volatile data storage. DataStoreInit() also takes care of
    // initializing the onboard data store to the current parameter values so all subsequent calls
    // to DataStoreLoadAllParameters() should work.
    if (!DataStoreInit()) {
        FATAL_ERROR();
    }

    // Initialize ECAN1
    Ecan1Init(F_OSC, NODE_CAN_BAUD);

    // Set up the ADC
    Adc1Init();

    // Set up a timer at F_timer = F_OSC / 2 / 256.
    OpenTimer2(T2_ON & T2_IDLE_CON & T2_GATE_OFF & T2_PS_1_256 & T2_32BIT_MODE_OFF & T2_SOURCE_INT, UINT16_MAX);
    ConfigIntTimer2(T2_INT_PRIOR_1 & T2_INT_OFF);

    // Finally perform the necessary pin mappings:
    PPSUnLock;

#ifdef __dsPIC33FJ128MC802__
    // To enable ECAN1 pins: TX on 7, RX on 4
    PPSOutput(OUT_FN_PPS_C1TX, OUT_PIN_PPS_RP7);
    PPSInput(IN_FN_PPS_C1RX, IN_PIN_PPS_RP4);

    // To enable UART1 pins: TX on 11, RX on 13
    PPSOutput(OUT_FN_PPS_U1TX, OUT_PIN_PPS_RP11);
    PPSInput(IN_FN_PPS_U1RX, IN_PIN_PPS_RP13);
#elif __dsPIC33EP256MC502__
    // To enable ECAN1 pins: TX on 39, RX on 36
    PPSOutput(OUT_FN_PPS_C1TX, OUT_PIN_PPS_RP39);
    PPSInput(IN_FN_PPS_C1RX, IN_PIN_PPS_RP36);

    // To enable UART1 pins: TX on 43 (B11), RX on 45 (B13)
    PPSOutput(OUT_FN_PPS_U1TX, OUT_PIN_PPS_RP43);
    PPSInput(IN_FN_PPS_U1RX, IN_PIN_PPS_RPI45);

    // To enable UART2 pins: TX on 40 (B8), RX on 41 (B9)
    PPSOutput(OUT_FN_PPS_U2TX, OUT_PIN_PPS_RP40);
    PPSInput(IN_FN_PPS_U2RX, IN_PIN_PPS_RP41);
#endif
    PPSLock;

    // And specify input/output settings for digital I/O ports:
    // A3 (output): Red LED on the CANode, blinks at 2Hz when the system is in reset, and is solid when the system hit a fatal error, otherwise off.
    _TRISA3 = OUTPUT;
    // A4 (output): Amber LED on the CANode, blinks at 1Hz for status.
    _TRISA4 = OUTPUT;
    // B12 (output): Amber automode LED on the CANode Primary Shield, on when system is autonomous, blinking at 4Hz when in manual override, and off otherwise.
    _TRISB12 = OUTPUT;
    // B15 (output): Amber GPS LED on the CANode Primary Shield, on when GPS is active & receiving good data.
    _TRISB15 = OUTPUT;

    /// At this point all hardware has been initialized.

    // Initialize the MAVLink communications channel
    MavLinkInit();

    // Finally initialize the controller model (generated MATLAB code)
    controller_initialize();

    // Report on system status now that initialization is complete.
    MavLinkSendStatusText(MAV_SEVERITY_INFO, "Finished initialization.");

    // Alert the operator to how much bandwidth will be used for each channel
    TransmitChannelUsage();

    // Broadcast the current mission item. This is useful if the controller has been power-cycled.
    // In that case, if the system had been running off the built-in default missions, the only
    // thing that QGC will have out of date is the current mission item. This fixes that case. If
    // the waypoints are out-of-date, nothing can be done about that, as the mission protocol is a
    // pull-only protocol.
    MavLinkSendCurrentMission(0);

    // Track the last error state that we were in. Used for triggering events on changes
    static uint16_t lastErrorState = 0;

    // Run system tasks when a timer interrupt has been triggered.
    while (true) {

        // Process incoming ECAN messages. This is done continuously. We may get multiple of the
        // same message between our 100Hz primary controller ticks, so data may be overridden,
        // but that doesn't really matter.
        ProcessAllEcanMessages();

        // Check for any errors on the ECAN peripheral:
        EcanStatus ecanErrors = Ecan1GetErrorStatus();
        if (nodeStatus & PRIMARY_NODE_STATUS_ECAN_TX_ERR) {
            if (!ecanErrors.TxError && !ecanErrors.TxBufferOverflow) {
                nodeStatus &= ~PRIMARY_NODE_STATUS_ECAN_TX_ERR;
            }
        } else {
            if (ecanErrors.TxError || ecanErrors.TxBufferOverflow) {
                nodeStatus |= PRIMARY_NODE_STATUS_ECAN_TX_ERR;
            }
        }
        if (nodeStatus & PRIMARY_NODE_STATUS_ECAN_RX_ERR) {
            if (!ecanErrors.RxError && !ecanErrors.RxBufferOverflow) {
                nodeStatus &= ~PRIMARY_NODE_STATUS_ECAN_RX_ERR;
            }
        } else {
            if (ecanErrors.RxError || ecanErrors.RxBufferOverflow) {
                nodeStatus |= PRIMARY_NODE_STATUS_ECAN_RX_ERR;
            }
        }

        // Turn on the GPS indicator LED depending on the GPS status.
        if (lastSensorAvailability.gpsEnabled && !sensorAvailability.gps.enabled) {
            lastSensorAvailability.gpsEnabled = false;
        } else if (!lastSensorAvailability.gpsEnabled && sensorAvailability.gps.enabled) {
            lastSensorAvailability.gpsEnabled = true;
        }

        // Set the GPS invalid status bit when it's no longer active
        if (lastSensorAvailability.gpsActive && !sensorAvailability.gps.active) {
            nodeErrors |= PRIMARY_NODE_STATUS_GPS_INVALID;
            lastSensorAvailability.gpsActive = false;
        } else if (!lastSensorAvailability.gpsActive && sensorAvailability.gps.active) {
            nodeErrors &= ~PRIMARY_NODE_STATUS_GPS_INVALID;
            lastSensorAvailability.gpsActive = true;
        }

        // Set the GPS disconnected error bit when the GPS has been inactive for too long.
        if (nodeErrors & PRIMARY_NODE_RESET_GPS_DISCONNECTED) {
            if (sensorAvailability.gps.active) {
                nodeErrors &= ~PRIMARY_NODE_RESET_GPS_DISCONNECTED;
            }
        } else {
            if (nodeSystemTime - sensorAvailability.gps.last_active >= GPS_DISCONNECTION_TIME) {
                nodeErrors |= PRIMARY_NODE_RESET_GPS_DISCONNECTED;
            }
        }
        if (lastSensorAvailability.gpsActive && !sensorAvailability.gps.active) {
            nodeErrors |= PRIMARY_NODE_STATUS_GPS_INVALID;
            lastSensorAvailability.gpsActive = false;
        } else if (!lastSensorAvailability.gpsActive && sensorAvailability.gps.active) {
            nodeErrors &= ~PRIMARY_NODE_STATUS_GPS_INVALID;
            lastSensorAvailability.gpsActive = true;
        }

        // If we ever lose contact with the ACS300, assume it's an e-stop condition.
        if (lastSensorAvailability.propEnabled && !sensorAvailability.prop.enabled) {
            nodeErrors |= PRIMARY_NODE_RESET_ESTOP_OR_ACS300_DISCON;
            lastSensorAvailability.propEnabled = false;
        } else if (!lastSensorAvailability.propEnabled && sensorAvailability.prop.enabled) {
            nodeErrors &= ~PRIMARY_NODE_RESET_ESTOP_OR_ACS300_DISCON;
            lastSensorAvailability.propEnabled = true;
        }

        // And if the rudder node disconnects, set the uncalibrated reset line. There's no need to perform
        // the inverse check when it becomes active again, because that will be done when the CAN message
        // is received.
        if (lastSensorAvailability.rudderEnabled && !sensorAvailability.rudder.enabled) {
            nodeErrors |= PRIMARY_NODE_RESET_RUDDER_DISCONNECTED;
            lastSensorAvailability.rudderEnabled = false;
        } else if (!lastSensorAvailability.rudderEnabled && sensorAvailability.rudder.enabled) {
            nodeErrors &= ~PRIMARY_NODE_RESET_RUDDER_DISCONNECTED;
            lastSensorAvailability.rudderEnabled = true;
        }

        /// RC Node:
        // The RC node is considered enabled if it's broadcasting on the CAN bus. If the RC node
        // ever becomes disabled, we note it. This isn't worthy of a system error or triggering RTB,
        // but it should be noted in the logs.
        if (lastSensorAvailability.rcNodeEnabled && !sensorAvailability.rcNode.enabled) {
            nodeStatus |= PRIMARY_NODE_STATUS_RC_NODE_DISCONNECTED;
            lastSensorAvailability.rcNodeEnabled = false;
        } else if (!lastSensorAvailability.rcNodeEnabled && sensorAvailability.rcNode.enabled) {
            nodeStatus &= ~PRIMARY_NODE_STATUS_RC_NODE_DISCONNECTED;
            lastSensorAvailability.rcNodeEnabled = true;
        }

        /// DST800:
        // This is required for the water speed reading, so if it's disconnected, we enter a reset
        // state.
        if (lastSensorAvailability.dst800Enabled && !sensorAvailability.dst800.enabled) {
            nodeErrors |= PRIMARY_NODE_RESET_DST800_DISCONNECTED;
            lastSensorAvailability.dst800Enabled = false;
        } else if (!lastSensorAvailability.dst800Enabled && sensorAvailability.dst800.enabled) {
            nodeErrors &= ~PRIMARY_NODE_RESET_DST800_DISCONNECTED;
            lastSensorAvailability.dst800Enabled = true;
        }

        /// IMU:
        // This is required for heading & turn rate, so if it's disconnected, we enter a reset state.
        if (lastSensorAvailability.imuEnabled && !sensorAvailability.imu.enabled) {
            nodeErrors |= PRIMARY_NODE_RESET_IMU_DISCONNECTED;
            lastSensorAvailability.imuEnabled = false;
        } else if (!lastSensorAvailability.imuEnabled && sensorAvailability.imu.enabled) {
            nodeErrors &= ~PRIMARY_NODE_RESET_IMU_DISCONNECTED;
            lastSensorAvailability.imuEnabled = true;
        }

        // If the RC node has stopped being active, it means that manual control is no longer being
        // enforced, so we clear that status and re-transmit the latest autonomous control commands.
        // Otherwise if the RC node becomes active while it's also enabled, then we have manual
        // override.
        if (lastSensorAvailability.rcNodeActive && !sensorAvailability.rcNode.active) {
            nodeErrors &= ~PRIMARY_NODE_RESET_MANUAL_OVERRIDE;

            // Output the command messages for this timestep even if they haven't changed,
            // because the primary controller is now back in control of the vessel.
            // FIXME: The storing of this data should not be done in the
            // *OutputControllerCommands() function.
            PrimaryNodeMuxAndOutputControllerCommands(currentCommands.autonomousRudderCommand,
                                                      currentCommands.autonomousThrottleCommand,
                                                      true);
            lastSensorAvailability.rcNodeActive = false;
        } else if (sensorAvailability.rcNode.enabled &&
                   !lastSensorAvailability.rcNodeActive && sensorAvailability.rcNode.active) {
            nodeErrors |= PRIMARY_NODE_RESET_MANUAL_OVERRIDE;
            lastSensorAvailability.rcNodeActive = true;
        }

        // If the rudder is no longer active, then the rudder is either in an error state or it's
        // undergoing calibration. Calibration can only be done while in manual mode, so triggering
        // a reset state here won't affect manual control but will trigger RTB in autonomous mode,
        // which is what's desired.
        if (lastSensorAvailability.rudderActive && !sensorAvailability.rudder.active) {
            nodeErrors |= PRIMARY_NODE_RESET_RUDDER_ERRORS;
            lastSensorAvailability.rudderActive = false;
        } else if (sensorAvailability.rudder.enabled &&
                   !lastSensorAvailability.rudderActive && sensorAvailability.rudder.active) {
            nodeErrors &= ~PRIMARY_NODE_RESET_RUDDER_ERRORS;
            lastSensorAvailability.rudderActive = true;
        }

        // Track transitions in rudder calibrating state.
        if (nodeErrors & PRIMARY_NODE_RESET_CALIBRATING) {
            if (!rudderSensorData.Calibrating) {
                nodeErrors &= ~PRIMARY_NODE_RESET_CALIBRATING;
            }
        } else {
            if (rudderSensorData.Calibrating) {
                nodeErrors |= PRIMARY_NODE_RESET_CALIBRATING;
            }
        }
        // Track transitions in rudder calibrated state.
        if (nodeErrors & PRIMARY_NODE_RESET_UNCALIBRATED) {
            if (rudderSensorData.Calibrated) {
                nodeErrors &= ~PRIMARY_NODE_RESET_UNCALIBRATED;
            }
        } else {
            if (!rudderSensorData.Calibrated) {
                nodeErrors |= PRIMARY_NODE_RESET_UNCALIBRATED;
            }
        }

        // If the GCS has been disconnected for too long, set an error flag
        if (nodeErrors & PRIMARY_NODE_RESET_GCS_DISCONNECTED) {
            if (MavLinkTimeSinceLastGcsMessage() < GCS_DISCONNECTION_TIME) {
                nodeErrors &= ~PRIMARY_NODE_RESET_GCS_DISCONNECTED;
            }
        } else {
            if (MavLinkTimeSinceLastGcsMessage() >= GCS_DISCONNECTION_TIME) {
                nodeErrors |= PRIMARY_NODE_RESET_GCS_DISCONNECTED;
            }
        }

        // Check for new MAVLink messages. We may get multiple of the
        // same message between our 100Hz primary controller ticks, so data may be overridden,
        // but that doesn't really matter, as we were losing that data anyways when we were
        // calling it at 100Hz.
        MavLinkReceive();

        // At this point we check to see if we're in an error state. If this error state is
        // different than what we were in before, and it's one of the error states that should
        // trigger the return-to-base functionality, then we trigger RTB mode. This is currently
        // done by cutting the throttle, and centering the rudder.
        // Note that RTB mode is only engaged when the vehicle is autonomous, otherwise primary
        // control should be allowed in almost every circumstance.
        // Transmitting these commands is done whenever the error state changes tomake sure that
        // if the rudder or propeller subsystems go offline and back online that they'll receive
        // the message and hopefully respond properly.
        if (nodeErrors != lastErrorState) {
            const uint16_t rtbErrors = nodeErrors & RTB_RESET_MASK;
            if (IS_AUTONOMOUS() && rtbErrors) {
                ActuatorsTransmitCommands(0.0, 0, true);

                // Make sure the operator is aware we're in RTB mode, but only announce it once.
                if (!(nodeErrors & PRIMARY_NODE_RESET_RTB)) {
                    char audioStr[] = "Enacting return-to-base protocol (reason 0x0000)";
                    audioStr[43] = int2hexchar((rtbErrors >> 12) & 0xF);
                    audioStr[44] = int2hexchar((rtbErrors >> 8) & 0xF);
                    audioStr[45] = int2hexchar((rtbErrors >> 4) & 0xF);
                    audioStr[46] = int2hexchar(rtbErrors & 0xF);
                    MavLinkSendStatusText(MAV_SEVERITY_EMERGENCY, audioStr);

                    nodeErrors |= PRIMARY_NODE_RESET_RTB;
                }
            }
            lastErrorState = nodeErrors;
        }

        // Trigger the 100Hz loop when the timer counts past the 0.01s mark.
        if (TMR2 >= F_OSC / 2 / 256 / 100) {
            TMR2 = 0; // We need to reset the timer counter BEFORE doing anything in here or it
                      // throws off our calculations.
            PrimaryNode100HzLoop();
        }
    }
}
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

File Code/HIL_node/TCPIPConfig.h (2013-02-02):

#ifndef TCPIPCONFIG_H
#define TCPIPCONFIG_H

// Use the DHCP server application from the TCPIP library. Note that this DHCP server only supports
// a single client.
#define STACK_USE_DHCP_SERVER

// Configure network settings like hostname, MAC, IP address, etc.
#define HOSTNAME			"UDP2SERIALBRIDGE"

#define MAC_BYTE1            (0x00)	// Use the default of 00-04-A3-00-00-00
#define MAC_BYTE2            (0x04)	// if using an ENCX24J600, MRF24WB0M, or
#define MAC_BYTE3            (0xA3)	// PIC32MX6XX/7XX internal Ethernet
#define MAC_BYTE4            (0x00)	// controller and wish to use the
#define MAC_BYTE5            (0x00)	// internal factory programmed MAC
#define MAC_BYTE6            (0x00)	// address instead.

#define IP_ADDR_BYTE1        (10ul)
#define IP_ADDR_BYTE2        (0ul)
#define IP_ADDR_BYTE3        (0ul)
#define IP_ADDR_BYTE4        (1ul)

#define MASK_BYTE1           (255ul)
#define MASK_BYTE2           (255ul)
#define MASK_BYTE3           (255ul)
#define MASK_BYTE4           (0ul)

#define GATE_BYTE1           IP_ADDR_BYTE1
#define GATE_BYTE2           IP_ADDR_BYTE2
#define GATE_BYTE3           IP_ADDR_BYTE3
#define GATE_BYTE4           IP_ADDR_BYTE4

#define PRIMARY_DNS_BYTE1	IP_ADDR_BYTE1
#define PRIMARY_DNS_BYTE2	IP_ADDR_BYTE2
#define PRIMARY_DNS_BYTE3	IP_ADDR_BYTE3
#define PRIMARY_DNS_BYTE4	IP_ADDR_BYTE4

#define SECONDARY_DNS_BYTE1	(0ul)
#define SECONDARY_DNS_BYTE2	(0ul)
#define SECONDARY_DNS_BYTE3	(0ul)
#define SECONDARY_DNS_BYTE4	(0ul)

// Use UDP.
#define STACK_USE_UDP

// Specify the server port to use for receiving UDP data messages.
#define UDP_SERVER_PORT 14550

// Specify the server port to use for transmitting UDP data messages.
#define UDP_CLIENT_PORT 14551

// Set the maximum number of UDP sockets. 3 covers DHCP, an input UDP socket, and an output UDP
// socket.
#define MAX_UDP_SOCKETS 3

// Specify that the stack will be used as a client. This is necessary for the IP_ADDRESS connection
// features of the UDPOpenEX() function.
#define STACK_CLIENT_MODE

// The max HTTP connections must also be specified even though we're not using it because the
// Microchip TCPIP stack is dumb.
#define MAX_HTTP_CONNECTIONS 1

#endif

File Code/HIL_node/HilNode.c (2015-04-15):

#include <stddef.h>
#include <stdint.h>

#include <xc.h>
#include <pps.h>
#include <timer.h>

#include "Hil.h"
#include "Acs300.h"
#include "MessageScheduler.h"
#include "Ecan1.h"
#include "Nmea2000.h"
#include "Rudder.h"
#include "Nmea2000Encode.h"
#include "Node.h"
#include "CanMessages.h"
#include "Timer2.h"
#include "Timer4.h"
#include "HilNode.h"
#include "Ethernet.h"

#ifndef NAN
#define NAN __builtin_nan("")
#endif

// Define some macros for setting pins as inputs or outputs using the TRIS pins.
#define OUTPUT 0
#define INPUT 1

// Declare some macros for helping setting bit values
#define ON  1
#define OFF 0

// Keep track of the processor's operating frequency.
#define F_OSC 80000000L

// Set processor configuration settings
#ifdef __dsPIC33FJ128MC802__
// Use internal RC to start; we then switch to PLL'd iRC.
_FOSCSEL(FNOSC_FRC & IESO_OFF);
// Clock Pragmas
_FOSC(FCKSM_CSECMD & OSCIOFNC_ON & POSCMD_NONE);
// Disable watchdog timer
_FWDT(FWDTEN_OFF);
// Disable JTAG and specify port 3 for ICD pins.
_FICD(JTAGEN_OFF & ICS_PGD3);
#elif __dsPIC33EP256MC502__
// Use internal RC to start; we then switch to PLL'd iRC.
_FOSCSEL(FNOSC_FRC & IESO_OFF);
// Clock Pragmas
_FOSC(FCKSM_CSECMD & OSCIOFNC_ON & POSCMD_NONE);
// Disable watchdog timer
_FWDT(FWDTEN_OFF);
// Disable JTAG and specify port 2 for ICD pins.
_FICD(JTAGEN_OFF & ICS_PGD2);
#endif

// Declare some constants for use with the message scheduler
// (don't use PGN or message ID as it must be a uint8)

enum {
    // Rudder messages
    SCHED_ID_RUDDER_ANGLE = 1,
    SCHED_ID_RUDDER_LIMITS, // For status bits

    // Throttle messages
    SCHED_ID_THROTTLE_STATUS,

    // RC node status messages
    SCHED_ID_RC_STATUS,

    // GPS messages
    SCHED_ID_LAT_LON,
    SCHED_ID_COG_SOG,
    SCHED_ID_GPS_FIX,

    // DST800 messages
    SCHED_ID_WATER_SPD,
    SCHED_ID_WATER_DEPTH,

    // HIL messages, specifically the NODE_STATUS message
    SCHED_ID_HIL_STATUS,

    // IMU messages
    SCHED_ID_IMU
};

// This variable is for tracking the status of the rudder subsystem. It broadcats status messages @
// 2Hz. Every time one of those messages is received, this counter is reset. The 100Hz Timer2 checks
// the counter every time it runs and if it is >= RUDDER_TIMEOUT_PERIOD, turns off the RUDDER_ACTIVE
// flag in `nodeStatus`. The timeout has been set to be 2 periods of time when the status message
// should have been received. Whenever a status message is received, that flag is also turned high.
// RUDDER_TIMEOUT_PERIOD is in units of the 100Hz timer, so 0.01s.
#define RUDDER_TIMEOUT_PERIOD 100
static uint16_t rudderTimeoutCounter = 0;

// This variable is used for determining when the propeller is active. Everytime a message is
// received, the counter is reset and if we haven't seem a prop message for 2 timesteps, we consider
// it inactive. Note that the ACS300 also goes inactive if the e-stop has been pulled.
#define PROP_TIMEOUT_PERIOD 2
static uint16_t propTimeoutCounter = 0;

// This variable is used for determining when the RC node is active. Everytime a status message is
// received, the counter is reset and if we haven't seem a prop message for 2 transmission periods,
// we consider it inactive.
#define RC_TIMEOUT_PERIOD 100
static uint16_t rcTimeoutCounter = 0;

// Used for checking if the DST800 is alive and broadcasting.
#define DST800_TIMEOUT_PERIOD 100
static uint16_t dst800TimeoutCounter = 0;

// Used for checking if the GPS is alive and broadcasting.
#define GPS_TIMEOUT_PERIOD 100
static uint16_t gpsTimeoutCounter = 0;

// Used for checking if the IMU is alive and broadcasting.
#define IMU_TIMEOUT_PERIOD 100
static uint16_t imuTimeoutCounter = 0;

// Track the status of the rudder subsystem. Used to check if it's calibrated. If not, calibration
// is triggered when HIL mode is started. Bit 0 is 1 when it has been calibrated.
static uint16_t rudderStatus = 0;

// Flag for triggering a run of the primary loop. Set by the timer interrupt.
static bool runPrimaryLoop = false;

// Set up the message scheduler's various data structures.
#define ECAN_MSGS_SIZE 11
static uint8_t ids[ECAN_MSGS_SIZE] = {
    SCHED_ID_RUDDER_ANGLE,
    SCHED_ID_RUDDER_LIMITS,
    SCHED_ID_THROTTLE_STATUS,
    SCHED_ID_RC_STATUS,
    SCHED_ID_LAT_LON,
    SCHED_ID_COG_SOG,
    SCHED_ID_GPS_FIX,
    SCHED_ID_WATER_SPD,
    SCHED_ID_WATER_DEPTH,
    SCHED_ID_HIL_STATUS,
    SCHED_ID_IMU
};
static uint16_t tsteps[ECAN_MSGS_SIZE][2][8] = {};
static uint8_t mSizes[ECAN_MSGS_SIZE];
static MessageSchedule sched = {
    ECAN_MSGS_SIZE,
    ids,
    mSizes,
    0,
    tsteps
};

// Declare some function prototypes
void SetPrimaryLoopFlag(void);

int main()
{
    /// First step is to move over to the FRC w/ PLL clock from the default FRC clock.
    // Set the clock to 79.84MHz.
    PLLFBD = 63; // M = 65
    CLKDIVbits.PLLPOST = 0; // N1 = 2
    CLKDIVbits.PLLPRE = 1; // N2 = 3

    // Initiate Clock Switch to FRM oscillator with PLL.
    __builtin_write_OSCCONH(0x01);
    __builtin_write_OSCCONL(OSCCON | 0x01);

    // Wait for Clock switch to occur.
    while (OSCCONbits.COSC != 1);

    // And finally wait for the PLL to lock.
    while (OSCCONbits.LOCK != 1);

    // Initialize everything
    HilNodeInit();

    // We continually loop through processing CAN messages and also HIL messages.
    while (true) {
        CanReceiveMessages();
        HilReceive();

        // Also execute the main execution loop at 100Hz.
        if (TMR2 >= F_OSC / 2 / 256 / 100) {
            TMR2 = 0; // We need to reset the timer counter BEFORE doing anything in here or it
                      // throws off our calculations.
            HilNodeTimer100Hz();
        }
    }
}

void HilNodeInit(void)
{
    // Set a unique node ID for this node.
    nodeId = CAN_NODE_HIL;

    // And configure the Peripheral Pin Select pins:
    PPSUnLock;
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

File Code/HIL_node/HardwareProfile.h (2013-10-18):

#ifndef HARDWARE_PROFILE_H
#define HARDWARE_PROFILE_H

#include <xc.h>

// Create a PIC dependant macro for the maximum supported internal clock in Hz.
#define MAXIMUM_PIC_FREQ		(80000000ul)

// These directly influence timed events using the Tick module.  They also are used for UART and SPI baud rate generation.
// These all return units of Hz.
#define GetSystemClock()		(MAXIMUM_PIC_FREQ)
#define GetInstructionClock()	(GetSystemClock()/2)
#define GetPeripheralClock()	(GetSystemClock()/2)

// ENC28J60 I/O pins
// The chip-select line is a standard digital output
#define ENC_CS_TRIS			(TRISBbits.TRISB15)
#define ENC_CS_IO			(LATBbits.LATB15)

// SPI SCK, SDI, SDO pins are automatically controlled by the SPI2 module
#define ENC_SPI_IF			(IFS2bits.SPI2IF)
#define ENC_SSPBUF			(SPI2BUF)
#define ENC_SPISTAT			(SPI2STAT)
#define ENC_SPISTATbits		(SPI2STATbits)
#define ENC_SPICON1			(SPI2CON1)
#define ENC_SPICON1bits		(SPI2CON1bits)
#define ENC_SPICON2			(SPI2CON2)

#endif // HARDWARE_PROFILE_H

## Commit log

2009-05-18 Implemented rudder forces and moments. Currently unstable at rudder angles != 0.
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2009-07-15 Finished RC model for boat. Uses a throttle and rudder channel to control the boat's rudder and propeller speed. Includes a failsafe in case of controller disconnection.
2009-07-21 Code should be working for communication with the boat and running all inputs/outputs besides the hall effect sensors to the boat. Serial interface doesn't work when connected to the boat using a reg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
2009-07-21 Changed input pins for hall effect sensors so that they no longer use the Explorer16 buttons and now use inputs off the breakout board.
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2009-07-22 Fixed mapping of ADC values from rudder position pot to be similar to PWM readings: 0-1023 with 0 being port and 1023 being starboard.
2009-07-22 Fixed input mapping so that values matched better between rudder position sensor and radio control receiver. Changed logic to be slightly more intuitive.
2009-07-23 - Cleaned up model slightly - Remapped ADC input to be more appropriately scaled Still doesn't work!
2009-07-23 Provides code to read from IC1 and IC2 and zeroing after a short timeout so that DC signals don't provide PWM values.
2009-07-23 - Fixed limit values for rudder. - Fixed direction output. - Rudder terns hard to port when transmitter is on and not certain why right now.
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2009-08-07 - Fixed various problems with the waypoint control model such that it now works for the one sample location I have. - Boat now chooses shortest rotation path to given point instead of always rotation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
    Model correctly slows to land on top of the destination location declared in boat_constants.m
    Model still needs further testing with other points.
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2010-04-15 Performed a major reorganization of the code to be more concise and easier to read. These changes are based off of the organization Mariano used for the autopilot. I removed a lot of code dealing wit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
2010-04-15 Converted local XY coordinate frame into latitude/longitude. This hasn't fixed the power model however, so some digging into that is required.
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2010-04-29 Added waypoint_control code to basic_model.mdl. I've made a few improvements to the code during this process: - A PID block from SLUGS is used for rudder control (currently only proportional control)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
2010-04-29 Added PID controller to throttle. Boat overshoots, but that can be fixed via altering coefficients.
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2010-05-25 Corrected optimal roll calculations to use the reference frame defined in SNAME 1950. All local reference frame calculations are now done in this reference frame. Also further specified global headin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
2010-05-25 Conversion into local spherical coordinates from global ones for the solar position didn't adjust the zenith angle. The new angle should be pi - zenith because of how the z-axis is defined as down in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
2010-05-29 Removed sun_position_test.m from tests.mdl and modified sun_position_test.m to be correct for testing it instead. - Was running into an infinite recursion problem with slUnit and matlab function call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
2010-06-29 Calculations no longer convert through ECEF to determine current LLA from local coordinates.
2010-06-30 Switched from LLA global positioning to working solely in local tangential plane. TODO: Fix charging code to still calculate proper charge calculations.
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2010-07-07 Found problem with heading/velocity vector being incorrect. Switched position to a vector and now it seems to be working correctly. Made some improvements to PlotTrack.m by using quiver() to plot the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
2010-07-08 Started to implement Phase 2 of the waypoint controller. Currently everything looks reasonable but Matlab won't compile it due to an algebraic loop.
2010-07-09 Fixed the algebraic loop by inserting a time delay with the Memory block. I should check with Mariano or Gabe to confirm this is the "correct" way to do this.
    I also modified PlotTrack.m to spit out some better looking plots.
2010-07-09 Fixed bug from previous commit. The signs on the rudder deflection for maximum lateral acceleration were switched. Minor fixes to PlotTrack.m also.
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2010-07-14 Completed the restoration of charge calculations. (bug was in the conversion of degrees to radians) Fixed sun_position_test.m to work properly. (pretty useless, but while it's here it should at least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
2010-07-20 Fixed rudder bug from previous commit by increasing rudder response to absurd levels. This NEEDS to be fixed, but at least now the sim is still usable, if unrealistic.
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2010-08-28 Fixed struct element reference error.
    [commProtocol.c]
2010-08-28 Ballast position is now a uint16 to correspond with the sensor input from an ADC that would spit that out. - The position is translated to/from -1..1 range using the same code as the rudder position 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
    [commProtocol.c]
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2010-08-30 Modified the 3rd state in the commProtocol message parser to be correct. I'm not certain what it was doing before.
    [commProtocol.c]
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2010-09-07 Important part of this commit is that HIL is now working. Vehicle oscillates around true path, but that's probably a baud rate issue. The trigger signal is also not properly transmit, so speed update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
    - Standardized getters/setters of various structs in commProtocol to use uint8 byte vectors.
    - RS232 TX/RX blocks are now wrapped in enable blocks so that straight-up simulation proceeds quickly.
    - The command struct in commProtocol is now much clearer.
    - There was a bug in the throttle command generation which is now fixed.
    - Custom code has been replaced by the pack/unpack blocks from the xPC Blockset to handle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
    [commProtocol.c]
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2010-09-15 Added uart2_rx for handling the reception of UART2's incoming data stream. This code doesn't actually compile within Simulink as the UART2 RX interrupt is generated by Lubin's blockset anyways. Code 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
    This model successfully communicates with the off-site dsPIC with < 300ms latency. This gives reasonable performance though state estimation isn't currently good enough to handle the slow update of position as it is completely reliant on GPS data at this point.
    [commProtocol.c]
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2010-09-16 uart2 is now completely self-contained. All parsing code code in gps.c and commProtocol.c uses the FIFOs defined in uart2.c, however.
    code_gen.mdl can now correctly switch between GPS parsing and HIL parsing. I still have not coded the baud rate changing code necessary for this to work, but that's the last change required.
    [commProtocol.c]
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2010-09-19 - Fixed a compilation warning - The total tally of successfully received & parsed messages is now stored in a global variable. Useful for debugging.
    [commProtocol.c]
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2010-09-29 Modified code_gen and supporting code to support the newData signal in the GPS struct. Updated code_gen to perform HIL with estimator code. I believe I'm missing code from my laptop repo as the boat 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
    [commProtocol.c]
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2010-09-30 Revert "Created trusses for bowline and perpendicular bowline."
    This reverts commit 49bd1817c5a73f20ec73628c00304df3296ec54f.
    [Bowline truss.SLDPRT, Cross-truss.SLDPRT]
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2010-09-30 Added perpindicular truss. Also fixed dimensions in Bowline truss for the sensor scaffold crossbar.
    [Bowline truss.SLDPRT, Perpendicular truss.SLDPRT, Truss.SLDPRT]
2010-09-30 Added slots so each truss fits into each other one. Slots have been added to the outside, also, so that can be stabilized too.
    [Bowline truss.SLDPRT, Perpendicular truss.SLDPRT]
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2010-10-01 Reworked both truss designs from scratch to get symmetry working. - Also thickened base support. - Moved zip-tie slots down to improve durability. - Fixed measurements so they should be correct.
    [Bowline truss.SLDPRT, Perpendicular truss.SLDPRT]
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2010-10-13 - The newGpsSignal generated for the autonomous controller in simulation is now transmit to the controller in HIL mode. This required modifications to both code_gen, Boat_sim, and commProtocol.*. - T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
    [commProtocol.c]
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2010-11-01 Added GPS baud rate and sentence configuration to the initialization routine in uart2.c. NOTE: This code currently fails. This may be because of the baud rate issues I ran into when trying to receive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
    [commProtocol.c]
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2010-11-16 Updated a couple of errors to the Xtend devboard: - Removed +5V connection to pin 9 on the DE9 connector - Added a GND connection on pin 5 on the DE9 connector - Switch VCC and GND connections to the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
    [board.PcbDoc, schematic.SchDoc]
2010-11-19 Last revision didn't have the Vcc line to the radio routed, this has been fixed.
    [board.PcbDoc]
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2011-04-19 - Added clearGpsData() to gps.c - Added clearSensorData() to commProtocol.c - Modified the gpsData struct to use "alt" instead of "height" - Extended the reset signal so that it cleared some more sto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
    [commProtocol.c]
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2011-04-24 Fixed an off-by-one error in the checkAndBuildMessage() function. Seems to work fine both before and after, which is weird.
    [commProtocol.c]
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2011-06-16 Revert "Moved auxiliary code to Lib/*."
    This reverts commit 11354368d9bd4207c22f567c3da8a79079b36a4b.
    [commProtocol.c]
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2011-07-15 Updated HIL in Boat_sim.mdl to transmit the message size with the packet. This allows for simpler and more robust checking logic. commProtocol.c/h was modified to check that the message size was righ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
    [commProtocol.c]
2011-07-16 commProtocol.c: - Added a counter for the number of times a message failed parsing. (untested) - Changed module-level variables to be static.
    [commProtocol.c]
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2011-07-18 Updated code_gen.mdl to output the rudder angle in radians over UART1. - Required a change in commProtocol.c as well. Updated the groundstation code to parse out the extra float and display it. It do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
    [commProtocol.c]
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2011-07-20 Added readings from the TC1047A temperature sensor onboard the Explorer16 to the outgoing telemetry to the groundstation. Note: Lubin's blockset currently has a bug. For this code to work properly, y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
    [commProtocol.c]
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2011-07-25 I've added a uint8 ordering byte to the outgoing state telemetry. Since messages are dropped over this broadcast knowing which ones are missing will help me piece together the data that we did record.
    [commProtocol.c]
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2011-07-27 Refactored the message parsing code within Boat_sim.mdl to match that in commProtocol.c. Fixed a small bug in commProtocol.c that deals with the message length.
    [commProtocol.c]
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2011-08-01 Groundstation - Added the rudder angle command display - The rudder angle command is recorded.
    code_gen.mdl
    - Added telemetry output of the commanded rudder angle, either the autonomous or manual one depending on the mode.
    - Added proportional position control to the rudder angle over manual control.
    - The throttle position is now averaged over 10 samples. This has smoothed the RC input quite a bit.
    NOTE: The rudder range under manual control ranges from about 39 degrees to -44 degrees so it doesn't completely span the full range. I'm calling it good enough for now.
    ANOTHER NOTE: When under autonomous control, the actual rudder angle jumps around quite a bit. This should be looked int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
    [commProtocol.c]
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2011-09-06 Added sensor feedback for the rudder position. This allows for better onboard HIL simulations that use the real rudder and rudder sensors. Previous runs with the onboard rudder sensors were incorrect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
    [commProtocol.c]
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2011-09-10 Switched the placement of the ACS300 motor driver board and the Explorer16 board to account for shorter motor and Hall effect sensor cables on the replacement propeller motor.
    [mountingboard.DXF, mountingboard.SLDDRW, mountingboard.SLDPRT]
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2011-11-07 Added the schematic for the protection board for the WSO100. This should prevent the boat deck or other things damaging the WSO100 (I hope).
    [WSO100 Guard.DXF, WSO100 Guard.SLDDRW, WSO100 Guard.SLDPRT]
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2011-12-09 Created a small stub mast for mounting the WSO100 wind/air sensor. This can replace the full-size aluminum mast in most testing situations.
    [Assembly.DXF, Assembly.SLDASM, Assembly.SLDDRW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]
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2012-01-11 Removed the archaic SensorData and ActuatorData struct from commProtocol.c. Added Rudder.c for handling storage of the rudder sensor data. All input data is now stored within structs in C, both in co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
    NOTE: This currently doesn't work with the old groundstation and I'm not sure why!
    [commProtocol.c]
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2012-02-03 Added the gps_node.mdl I'm using for my GPS-to-CAN dsPIC33f. I added a GpsNewData() function to check for new GPS data. Fixed a few various bugs/unnecessary code bits.
    [main.c]
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2012-02-12 Switched GPS data to receive from Maretron's GPS200 unit over NMEA2000. Refactored a bunch of code to use fixed-length data types from <inttypes.h> Reduce the GPS bus in use within Simulink to only c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
    [commProtocol.c]
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2012-06-18 Multiple style fixes to the code base. Multiple compilation warning fixes when compiled on the highest warning settings. The code that keeps track of what sensors are online and which are receiving g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
    [commProtocol.c]
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2012-08-26 * Converted the onboard code (both MATLAB and C) to use the new GPS datatypes that were updated in the simulator within the last few commits. * Added a new status bit for the boat for whether the RC 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
    [commProtocol.c]
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2012-10-22 Fixed compilation of the basic_model using the new CircularBuffer and ECAN code built on top of it.
    [commProtocol.c]
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2012-11-10 Fixed bug with HIL onboard. Arose from circular buffer changes.
    [commProtocol.c]
2012-11-10 HIL messages are now correctly received by the computer. HIL is still not working, however.
    [commProtocol.c]
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2012-11-14 Fixed some indentation in commProtocol.c.
    [commProtocol.c]
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2012-11-30 HIL Node: * Refactored/renamed most of the code. * Two-way communications with the new Boat_sim.mdl work, though latency is up around 1s. Primary Node: * Refactored some code and improved includes. B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
    [HilNode.c]
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2012-12-01 Primary node: * Updated to use new UART library HIL node: * Now communicates all CAN messages that puts the primary node out of reset. Boat sim: * Now communicates via serial.
    [CommProtocol.c]
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2012-12-01 Primary node: * Refactored to use the new autonomous controller that doesn't do actuator output mapping or have ballast code. * Move the RevoGS library to Libs where it should be. * Removed the CommP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
    [CommProtocol.c, PrimaryNode.c]
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2012-12-14 HIL Node: * Rewrote the HIL node in straight C to improve latency. * The node no longer does the necessary CAN interfacing, that was removed for testing and will need to be readded. * A pulse is trig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
    [HilNode.c]
2012-12-14 Libs: * Pulled in the code from the ECAN library and refactored it somewhat, mostly removing MATLAB-style functions. HIL Node: * Reworked all HIL code to use these new/modified libs.
    [HilNode.c]
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2012-12-16 Primary node: * Reverted back to the old ECAN library. I need to figure out what that * was about: incoming ECAN1 messages were corrupted. Notes: * HIL works! Not very robustly, but we're getting the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
    [PrimaryNode.c]
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2012-12-19 Rudder node: * Fixed transmission of rudder angle to properly specify invalid data.
    [RudderNode.c]
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2013-01-17 CAD: * The electronics mountingboard no longer has the 2035 stepper motor drive mounted to it so it was removed.
    [mountingboard.SLDPRT]
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2013-01-20 Primary node: * Minor documentation fix.
    [PrimaryNode.c]
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2013-01-23 RudderNode: * Updated main source files includes so that they're "more correct".
    [RudderNode.c]
2013-02-02 Primary node now uses Packing.h for packing/unpacking data. GPS position processing has been improved so that the fix is now read properly and accounted for when reading lat/lon. Basically cog/sog, l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
    [PrimaryNode.c]
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2013-02-02 Fixed LED blinking bug in HIL node code. LED now blinks slowly when not in HIL and quickly when in it.
    [HilNode.c]
2013-02-02 Added preliminary code for integrating with the rudder node. When the rudder node is active and broadcasting, the HIL node no longer simulated being the rudder node and allows the actual one to be.
    [HilNode.c]
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2013-02-16 This commit finishes the conversion to the new NODE_STATUS CAN message format. I forgot to update all the calls to CanMessageDecodeStatus(). That's now fixed.
    [HilNode.c]
2013-02-16 Modified the Primary Node so that actuator commands are only output if the device is not in reset. Additionally did some magic number cleanup and removed the MODE_RC_DISCON parameter.
    [PrimaryNode.c]
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2013-04-30 Fixed errors with CANode shields have too much clearance around board edges.
    [control.brd, power_sense_shield.brd, rudder_shield.brd]
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2013-08-11 Moved the GPS_DISCONNECT status flag, e-stop reset flag, and startup reset flag to C code for the primary node.
    [PrimaryNode.c]
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2013-08-11 Restored the missing status LED blinking functionality. Also moved the reset LED functionality to C.
    [PrimaryNode.c]
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2013-08-11 Attempted to move ADC code into C from Simulink. This was the last hurdle before moving out of Simulink altogether. This code doesn't work right yet, but I'm unsure why.
    [PrimaryNode.c]
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2013-10-18 Refactored the primary node to no longer use Lubin's blockset for generating C code.
    [PrimaryNode.c]
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2013-12-07 Modified the controller so that it no longer writes to the global internalVariables struct, and instead outputs all that internal data as an output variable struct. Also have the post-sim visualizati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
    [PrimaryNode.c]
2014-01-28 Updating PPS code to reflect bug fixes in XC16-1.21 compiler.
    [HilNode.c, PrimaryNode.c]
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2014-01-28 Fixed PrimaryNode.c to work on XC16 1.21. PPS and ADC macros in Microchip's peripheral lib changed. Also compiler warning fix.
    [PrimaryNode.c]
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2014-02-06 IMU node no longer requires MATLAB or the blockset.
    [ImuNode.c, main.c]
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2014-02-20 Primary node: Removed code that triggered a UART1 reset when B0 was pulled low.
    [PrimaryNode.c]
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2014-02-22 Imu node: Fixed Tokimec data processing.
    [ImuNode.c]
2014-02-22 Primary node: Fixed warning about improper datatype.
    [PrimaryNode.c]
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2014-02-25 Primary Node: Altered MAVLink output reset to reinit entire UART1 module.
    [PrimaryNode.c]
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2014-03-06 Primary node: Shorten the time it takes for MAVLink corruption to be detected.
    [PrimaryNode.c]
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2014-05-12 Mavlink Corruption Node: Created a test node for the MAVLink corruption issue. A subset of the Primary Node code. Currently just the MAVLink interface and backend data stores.
    [MavCorruptNode.c]
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2014-05-22 Code/PrimaryNode: Prevent the system time from overflowing.
    [PrimaryNode.c]
2014-05-22 Code/PrimaryNode: Initialize acutator commands to sane values. Prevents warnings when controller_custom() is commented out for debugging or if it never set a value.
    [PrimaryNode.c]
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2014-06-13 Primary node: Removed variables now unused because MAVLink corruption is no longer being detected.
    [PrimaryNode.c]
2014-06-13 Primary node: Actuator commands are retransmit when the secondary controller is no longer active. This lowers the latency of switching from the secondary controller back to the boat.
    [PrimaryNode.c]
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2014-10-23 MPU sampling is now correct.
    Currently using a heavy polling mechanism. Need to switch to an interrupt-driven version.
    [AttitudeNode.c]
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2014-11-04 Add the IMU CAN messages to the HIL node.
    All the other noise in this was a simple re-indentation by MPLAB X.
    [HilNode.c]
2014-11-08 Fixed bug with using integer exponentials in a float context.
    [PrimaryNode.c]
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2014-11-09 Correct comments on clock configuration.
    [PrimaryNode.c]
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2014-11-09 Forgot to convert to fixed-point for transmiting IMU data over CAN.
    [HilNode.c]
2014-11-10 Fix the primary node to actually run it's control loop at 100Hz instead of 95.
    Also fix a possible timing bug in other main()s.
    [HilNode.c, PrimaryNode.c, main.c]
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2014-11-13 Make the HIL node fail hard on ECAN failures.
    [HilNode.c]
2014-11-13 Refactor the ECAN error status function and add GetErrorCounts().
    Also refactor the PrimaryNode to use this new code and also output the error counts.
    [PrimaryNode.c]
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2014-11-19 Replaced old IMU mount with new in-boat one.
    [mount.SLDPRT]
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2014-12-15 Fix labeling error.
    [rudder_shield.brd]
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2015-02-09 OpenDMA1 was fixed in Microchip's Plib, so use it correctly now.
    [PrimaryNode.c]
2015-02-09 Update the Primary Node.
    Now we transmit the CONTROLLER_DATA message immediately after each control loop.
    Various spelling fixes.
    And indentation fixes.
    We don't transmit any non-essential messages.
    [PrimaryNode.c]
2015-02-13 Split the MAVLink streams for the groundstation and logger.
    Channel 0 is the groundstation and channel 1 is the logger.
    This has broken the parameter value output that was being used to transmit over to QGC which
    will be fixed shortly.
    Also UART2 is now used for the datalogger and mapped to the extra FTDI pinout on the PrimaryNode shield.
    [PrimaryNode.c]
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2015-02-19 Fix bug where the controller always thought the GPS data was new.
    [PrimaryNode.c]
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2015-02-27 Blink the GPS LED when its connected but doesn't have a fix.
    [PrimaryNode.c]
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2015-03-02 Enter reset when the groundstation is missing for >= 30s
    [PrimaryNode.c]
2015-03-02 Fix RESET/STATUS triggers not working correctly on startup.
    [PrimaryNode.c]
2015-03-02 Switch GPS disconnection to be an error state.
    [PrimaryNode.c]
2015-03-03 Add return to base functionality.
    This doesn't actually drive anywhere, but instead centers the rudder and kills the throttle.
    [PrimaryNode.c]
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2015-03-03 Add back the GPS_INVALID status bit but keep a GPS_DISCON reset bit.
    Also limit RTB functionality to GPS or GCS disconnections or e-stops.
    [PrimaryNode.c]
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2015-03-03 Fix setting the GPS_DISCONNECTED reset bit.
    [PrimaryNode.c]
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2015-03-07 Improve debugging output from the HIL node.
    Detect if the IMU, GPS, or DST800 are transmitting and sit in an error state if so.
    Make the internal code copy the PrimaryNode more closely for consistency.
    Don't output RC status messages when the RC node is connected.
    [HilNode.c]
2015-03-07 Make the RTB state a reset error and have a clear enable/disable path for it.
    The RTB flag is therefore a way to disable autonomous mode once an RTB criteria is met,
    but then even if those criteria go away, have it stay in reset. I want it to be this way
    so that I have to switch it to manual mode, check everything, and then re-enable autonomous
    mode.
    [PrimaryNode.c]
2015-03-07 When the rudder has disconnected, note that explicitly.
    The UNCALIBRATED error should be separate from whether the rudder is connected or not.
    [PrimaryNode.c]
2015-03-07 Add the reset logic for the DST800 and IMU.
    [PrimaryNode.c]
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2015-03-09 Correct setting/clearing of error bits.
    Simple copy/paste mistake.
    [PrimaryNode.c]
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2015-03-09 Allow for the primary controller to work even when the system is in a reset state.
    [PrimaryNode.c]
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2015-03-12 Correct the BearingToNextWaypoint function.
    [PrimaryNode.c]
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2015-03-19 Add audio output for crosstrack error and waypoint distance.
    Repeats every 30s after a waypoint transition while autonomous and not having errors.
    [PrimaryNode.c]
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2015-03-25 Add a check for the rudder motor not working correctly.
    [RudderNode.c]
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2015-03-26 Use new error reporting from the rudder to track when it's active.
    Also trigger RTB when the rudder goes inactive.
    [PrimaryNode.c]
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2015-03-26 Only allow engaging autonomous mode if no RTB errors exist.
    [PrimaryNode.c]
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2015-03-30 Add an e-stop error check to the rudder node.
    [RudderNode.c]
2015-03-30 Move processing changes in error states to C code.
    This was necessary for modifying the nodeErrors variable anywhere and still
    detecting changes.
    [RudderNode.c]
2015-03-30 Lower the sensitivity on the motor stall checking code.
    [RudderNode.c]
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2015-04-08 Fix output of comm channel bandwidth usage.
    [PrimaryNode.c]
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
